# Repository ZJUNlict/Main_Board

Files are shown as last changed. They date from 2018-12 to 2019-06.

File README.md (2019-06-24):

# Main_Board

ZJUNlict Main Board Design for the RoboCup Soccer Small-Size League https://zjunlict.cn/

The main board is designed to replace the [core board](https://github.com/ZJUNlict/Core_Board), [mother board](https://github.com/ZJUNlict/Mother_Board) and [motor driver board](https://github.com/ZJUNlict/Motor_Driver_Board) which is currently under testing. (The board is designed using [Altium Designer](https://www.altium.com/altium-designer/) 17.1)

**Sincere thanks for Team TIGERs Mannheim's [opensource electronics design](https://tigers-mannheim.de/index.php?id=65), which gives a mature seperate BLDC controller design with small footprint and relative low cost.**

The photos of the main board are shown below.

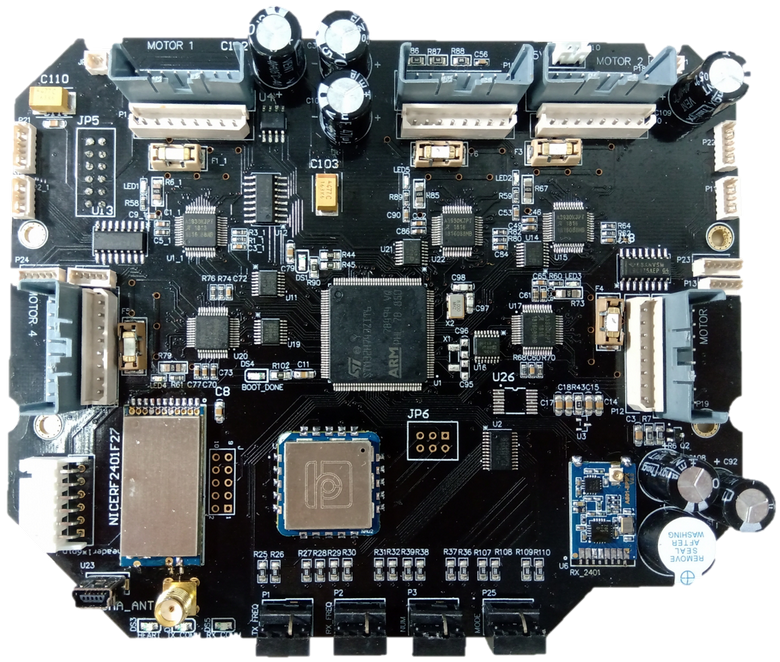
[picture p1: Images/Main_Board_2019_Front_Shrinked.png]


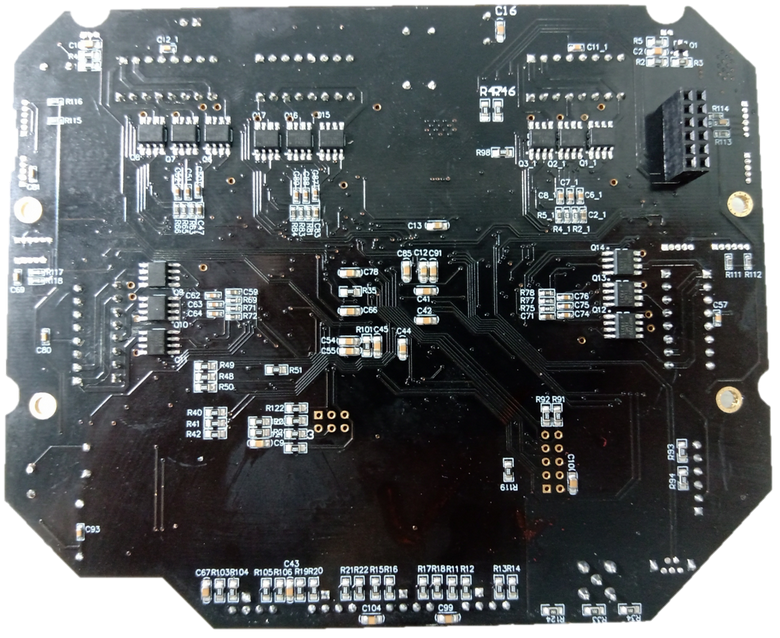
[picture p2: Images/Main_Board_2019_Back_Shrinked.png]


The main features are:

* STM32H743ZIT6 as the main controller with frequency up to 480MHz.
* Two nRF24L01P modules operate in different frequency handles package receiving and transmitting.
* An IO expansion chip PCA9539 reads rotary DIP switchs.
* Five BLDC controller chips A3930 controls five motors based on Team TIGERs Mannheim's design.
* Differential receiver chip SN65LBC175 receives encoder signal.
* AD converter chip ADS112C04IPWR process the current signal from A3930.
* Interface to external gyroscope, accelerometer, compass and optic flow chips. (IIC and SPI)

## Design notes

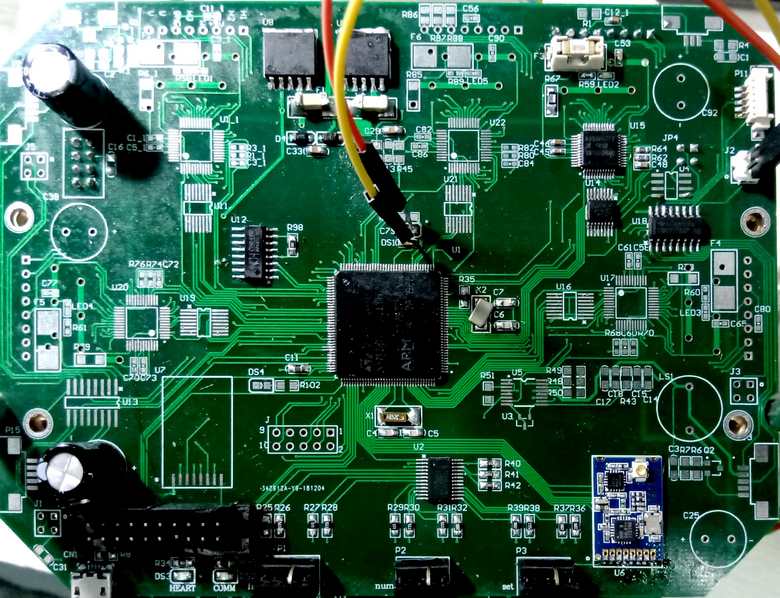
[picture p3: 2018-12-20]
Images/Main_Board_2_Shrinked.jpg

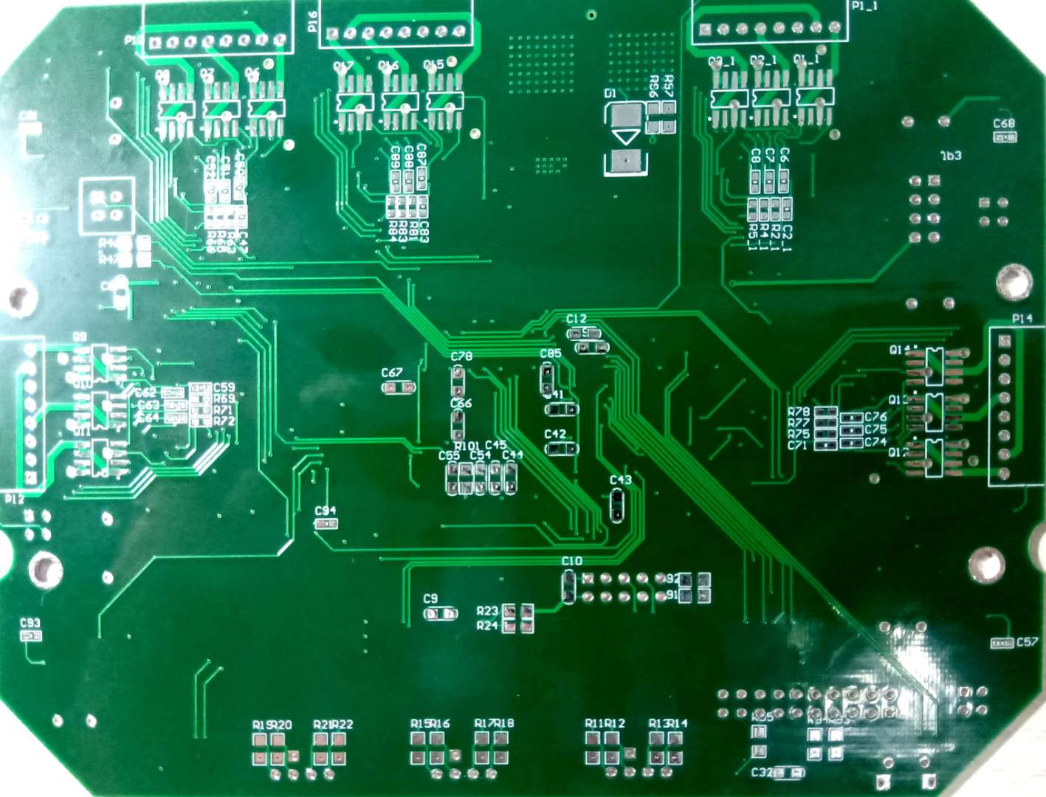
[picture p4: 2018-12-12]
Images/Main_Board_Back.jpg

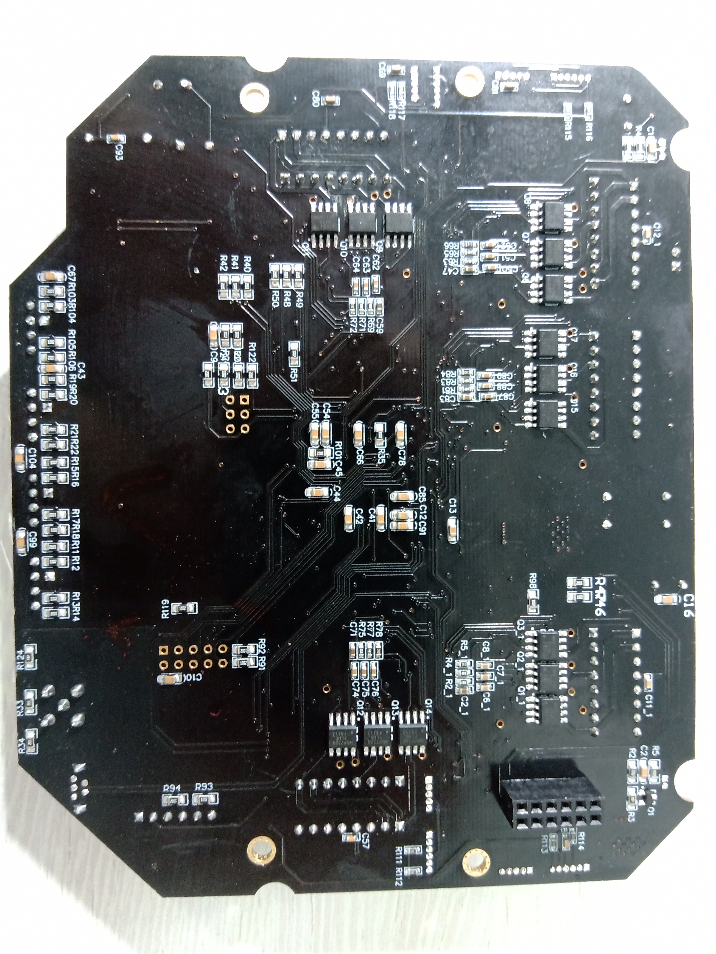
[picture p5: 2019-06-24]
Images/Main_Board_2019_Back.jpg

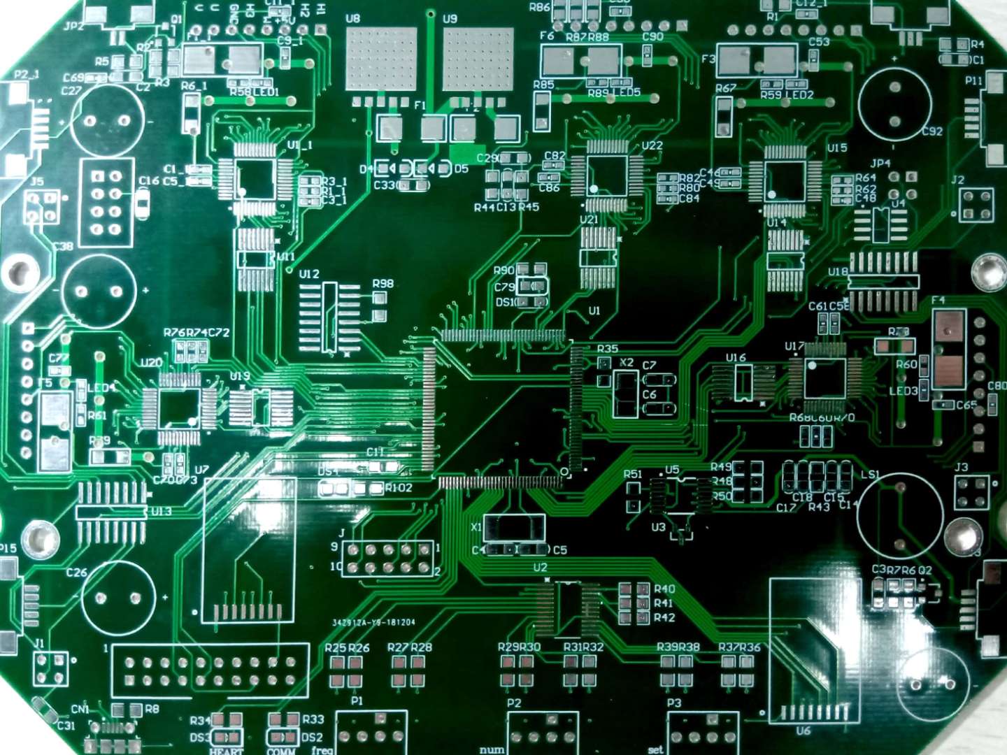
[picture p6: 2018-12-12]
Images/Main_Board_Front.jpg

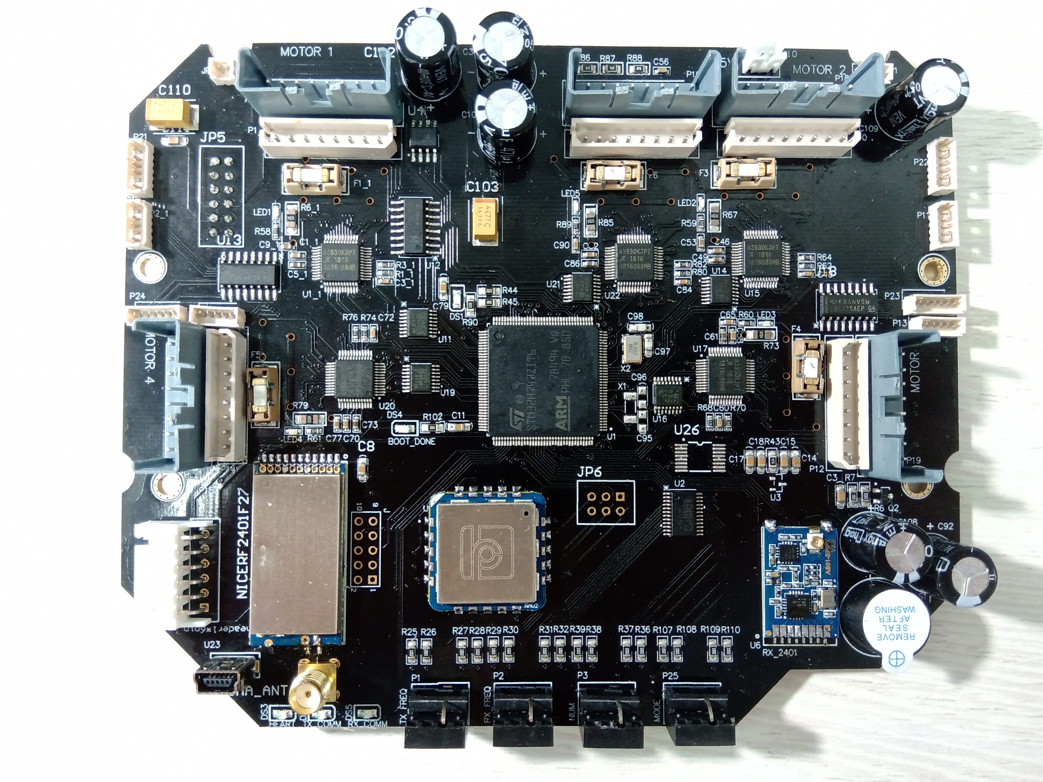
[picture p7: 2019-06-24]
Images/Main_Board_2019_Front.jpg

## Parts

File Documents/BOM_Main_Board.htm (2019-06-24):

Comment | Description | Designator | Footprint | LibRef | Quantity
0.1uf | Capacitor | C1, C2, C3, C8, C9, C10, C15, C16, C17, C18, C41, C42, C43, C44, C45, C54, C55, C66, C67, C78, C79, C85, C91, C99, C104, C111 | 0805C | Cap | 26
1uF | Capacitor | C1_1, C2_1, C9_1, C46, C47, C53, C58, C59, C65, C70, C71, C77, C82, C83, C90 | 0603C | Cap | 15
1nF | Capacitor | C3_1, C48, C60, C72, C84 | 0603C | Cap | 5
470nF | Capacitor | C5_1, C49, C61, C73, C86 | 0603C | Cap | 5
33nF | Capacitor | C6_1, C7_1, C8_1, C50, C51, C52, C62, C63, C64, C74, C75, C76, C87, C88, C89 | 0603C | Cap | 15
1uf | Capacitor | C11, C12, C14 | 0805C | Cap | 3
0.1uF | Capacitor | C11_1, C12_1, C56, C57, C68, C69, C80, C81, C93 | 0603C | Cap | 9
10uF | Capacitor | C13 | 0805C | Cap | 1
470uF | Polarized Capacitor (Radial) | C38, C92, C107, C108, C109, C112 | 470uF | Cap Pol1 | 6
2pf | Capacitor | C95, C96 | 0805C | Cap | 2
4.3pf | Capacitor | C97, C98 | 0805C | Cap | 2
CAP470 | 470uF电容贴片 | C103, C110 | CAPPM7360X200N | T523H477M016APE0707280 | 2
LED2 | Typical RED, GREEN, YELLOW, AMBER GaAs LED | DS1, DS3, DS4 | 0805D | LED2 | 3
LED1 | Typical RED, GREEN, YELLOW, AMBER GaAs LED | DS2, DS5 | 0805D | LED1 | 2
10A |  | F1_1, F3, F4, F5, F6 | FUSE_HEADER | FUSE | 5
header1*6pin | header1*6pin | header1*6pin | 1*6_2.5mm | header1*6pin | 1
10 |  | J | 10 | 10 | 1
1*2*2.5mm |  | J10 | 1*2_2.5mm | 1*2*2.5mm | 1
Header 3 | Header, 3-Pin | JP1 | SHDR3 | Header 3 | 1
Header 2 | Header, 2-Pin | JP2 | SHDR2 | Header 2 | 1
Header 4X2 | Header, 4-Pin, Dual row | JP5 | 2*6_2.5mm | Header 6X2 | 1
header6pin |  | JP6 | 2*3_2.5mm | header6pin | 1
led |  | LED1, LED2, LED3, LED4, LED5 | 0603_diode | led | 5
Buzzer | Buzzer | LS1 | Buzzer | Buzzer | 1
NICERF2401F27 |  | NICERF2401F27 | NICERF2401F27 | NICERF2401F27 | 1
COAX-M | RF Coaxial PCB Connector, MMCX; Thru-Hole, Vertical Mount Plug, 50 Ohm Impedance | P1, P2, P3, P25 | A6RV-161RS | COAX-M | 4
Header_8P | Used for Motor connection in ZJUNlict | P1_1, P8, P10, P12, P14 | 8P - WF25122 | Header_8P | 5
Header 5 | Header, 5-Pin | P2_1, P11, P13, P15 | SHDR5 | Header 5 | 4
安装孔 | Plug | P4, P5, P6, P7 | 安装孔-3.5-5 | Plug | 4
Header_8P | Used for Motor connection in ZJUNlict | P16, P17, P18, P19, P20 | SHDR8 | Header_8P | 5
Header 5 | Header, 5-Pin | P21, P22, P23, P24 | SHDR6 | Header 6 | 4
9013 | NPN General Purpose Amplifier | Q1, Q2 | SO-G3/Y1 | BC817-40 | 2
IRF8313 |  | Q1_1, Q2_1, Q3_1, Q6, Q7, Q8, Q9, Q10, Q11, Q12, Q13, Q14, Q15, Q16, Q17 | so-8 bg | SO-8 IRF8313 | 15
20K | Resistor | R1 | 0805R | Res1 | 1
47K | Resistor | R1_1, R62, R68, R74, R80 | 0603R | Res1 | 5
2.2K | Resistor | R2, R6 | 0805R | Res1 | 2
100K | Resistor | R2_1, R4_1, R63, R65, R69, R71, R75, R81, R83 | 0603R | Res1 | 9
1K | Resistor | R3, R7 | 0805R | Res1 | 2
10K | Resistor | R3_1, R5_1, R64, R66, R70, R72, R76, R78, R82, R84, R111, R112, R113, R114, R115, R116, R117, R118 | 0603R | Res1 | 18
100 | Resistor | R4 | 0805R | Res1 | 1
300 | Resistor | R5 | 0805R | Res1 | 1
0.02 | Resistor | R6_1, R67, R73, R79, R85 | 1206 10A | Res1 | 5
10k | Resistor, Resistor, Resistor, Resistor, Resistor, Resistor, Resistor, Resistor, Resistor, Resistor, Resistor, Resistor, Resistor, Resistor, Resistor, Resistor, Resistor, Resistor, Resistor, Resistor, Resistor, Resistor, Resistor, Resistor, Resistor, Resistor, Resistor, Resistor, Resistor, Resistor, Resistance, Resistance, Resistor, Resistor, Resistor, Resistor, Resistor, Resistor, Resistor, Resistor, Resistor, Resistor, Resistor, Resistor, Resistor, Resistor, Resistor, Resistor, Resistor, Resistor, Resistor, Resistor, Resistor, Resistor, Resistor | R11, R12, R13, R14, R15, R16, R17, R18, R19, R20, R21, R22, R23, R24, R25, R26, R27, R28, R29, R30, R31, R32, R35, R36, R37, R38, R39, R40, R41, R42, R46, R47, R48, R49, R50, R51, R91, R92, R93, R94, R98, R101, R103, R104, R105, R106, R107, R108, R109, R110, R119, R120, R121, R122, R123 | 0805R | Res1, Res1, Res1, Res1, Res1, Res1, Res1, Res1, Res1, Res1, Res1, Res1, Res1, Res1, Res1, Res1, Res1, Res1, Res1, Res1, Res1, Res1, Res1, Res1, Res1, Res1, Res1, Res1, Res1, Res1, SR0805, SR0805, Res1, Res1, Res1, Res1, Res1, Res1, Res1, Res1, Res1, Res1, Res1, Res1, Res1, Res1, Res1, Res1, Res1, Res1, Res1, Res1, Res1, Res1, Res1 | 55
3.3k | Resistor | R33, R34, R45, R90, R102, R124 | 0805R | Res1 | 6
470 | Resistor | R43 | 0805R | Res1 | 1
22k | Resistor | R44 | 0805R | Res1 | 1
10k |  | R58, R59, R60, R61, R89 | 0603 | res | 5
150K | Resistor | R77 | 0603R | Res1 | 1
5.1k |  | R86, R87, R88 | 0805 | res | 3
SMA_ANT |  | SMA_ANT | SMA_ANT | SMA_ANT | 1
MCU_LQFP144 |  | U1 | LQFP144_0R5_SKT | MCU_LQFP144 | 1
A3930 |  | U1_1, U15, U17, U20, U22 | LQFP-48 | LQFP 48 | 5
PCA9539_PW_24 | Remote 16-Bit I2C And SMBus, Low-Power I/O Expander With Interrupt Output, Reset & Config. Registers | U2 | PW24-L_pca9539 | PCA9539_PW_24 | 1
TL4050A10_DBZ_3 | Precision Micropower Shunt Voltage Reference | U3 | DBZ3-L | TL4050A10_DBZ_3 | 1
MC34152D | High Speed Dual MOSFET Driver | U4 | SO-G8 | MC34152D | 1
NRF2401P+ |  | U6 | NRF2401P+_zeyao | NRF2401P+ | 1
ADUM141D0BRQZ | Imported | U11, U14, U16, U19, U21 | RQ_16 | ADUM141D0BRQZ | 5
CH340B |  | U12 | SOP16 | CH340B | 1
SN65LBC175A-EP_16 | Quadruple 2-Input Positive-NAND Gates | U13, U18 | SOP16 | SN65LBC175A-EP_16 | 2
miniusb |  | U23 | miniusb 180 | miniusb | 1
LPMS-NAV2 | LPMS-NAV2 | U25 | LPMS-NAV2 | LPMS-NAV2 | 1
ADS112C04IPWR | Imported | U26 | TSSOP_PW0016A_ADS112C04 | ADS112C04IPWR | 1
32.768KHZ | Crystal | X1 | FC-255 | CRYSTAL | 1
8MHZ | Crystal or Oscillator | X2 | 5032 | ECS-80-18-30B-AGN-TR | 1

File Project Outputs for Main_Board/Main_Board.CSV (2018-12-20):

Bill of Material for
On 2018/12/20 at 20:23:41
Comment | Pattern | Quantity | Components
0.02 | 1206 10A | 5 | R6_1, R67, R73, R79, R85 | Resistor
0.1uF | 0603C | 10 | C11_1, C12_1, C56, C57, C68, C69, C80, C81, C93, C94 | Capacitor
0.1uF | 0805C | 33 | C2, C3, C4, C5, C6, C7, C8, C9, C10, C11, C12, C13, C15, C16, C17, C18, C29, C31, C32, C33, C41, C42, C43, C44, C45, C54, C55, C66, C67, C78, C79, C85, C91 | Capacitor
10 | 10 | 1 | J
100 | 0805R | 1 | R4 | Resistor
100K | 0603R | 5 | R2_1, R63, R69, R75, R81 | Resistor
1050170001 | Micro_USB | 1 | CN1
10A | FUSE_HEADER | 5 | F1_1, F3, F4, F5, F6
10K | 0603R | 10 | R3_1, R5_1, R64, R66, R70, R72, R76, R78, R82, R84 | Resistor
10K | 0805R | 46 | R8, R11, R12, R13, R14, R15, R16, R17, R18, R19, R20, R21, R22, R23, R24, R25, R26, R27, R28, R29, R30, R31, R32, R35, R36, R37, R38, R39, R40, R41, R42, R46, R47, R48, R49, R50, R51, R91, R92, R93, R94, R95, R96, R97, R98, R101 | Resistor
150K | 0603R | 5 | R4_1, R65, R71, R77, R83 | Resistor
1K | 0805R | 2 | R3, R7 | Resistor
1nF | 0603C | 5 | C3_1, C48, C60, C72, C84 | Capacitor
1uF | 0603C | 15 | C1_1, C2_1, C9_1, C46, C47, C53, C58, C59, C65, C70, C71, C77, C82, C83, C90 | Capacitor
1uF | 0805C | 1 | C14 | Capacitor
2.2K | 0805R | 2 | R2, R6 | Resistor
20 | 20SWD | 1 | 1
20K | 0805R | 3 | R1, R90, R102 | Resistor
22k | 0805R | 1 | R44 | Resistor
3.3k | 0805R | 1 | R45 | Resistor
300 | 0805R | 1 | R5 | Resistor
32.768KHZ | FC255_32.768K | 1 | X1 | Crystal
33nF | 0603C | 15 | C6_1, C7_1, C8_1, C50, C51, C52, C62, C63, C64, C74, C75, C76, C87, C88, C89 | Capacitor
3A | 2512r | 2 | F1, F2 | Resistor
4.7K | 603 | 5 | R58, R59, R60, R61, R89
4.7K | 805 | 3 | R86, R87, R88
4.7uF | 0805C | 1 | C1 | Capacitor
4 | 4 | 4 | J1, J2, J3, J5
470 | 0805R | 1 | R43 | Resistor
470nF | 0603C | 5 | C5_1, C49, C61, C73, C86 | Capacitor
470uF | 470uF | 5 | C25, C26, C27, C38, C92 | Capacitor
47K | 0603R | 5 | R1_1, R62, R68, R74, R80 | Resistor
510 | 0805R | 2 | R33, R34 | Resistor
8MHZ | 5320_8M | 1 | X2 | Crystal
9013 | SO-G3/Y1 | 2 | Q1, Q2 | NPN General Purpose Amplifier
A3930 | LQFP-48 | 5 | U1_1, U15, U17, U20, U22
ADS112C04IPWR | TSSOP_PW0016A_ADS112C04 | 1 | U5 | Imported
ADUM141D0BRQZ | RQ_16 | 5 | U11, U14, U16, U19, U21 | Imported
BA33DD0WHFP | HRP5_16TO5 | 1 | U9
BA50DD0WHFP | HRP5_16TO5 | 1 | U8
Buzzer | Buzzer | 1 | LS1 | Buzzer
CH340B | SOP16 | 1 | U12
COAX-M | A6RV-161RS | 3 | P1, P2, P3 | RF Coaxial PCB Connector, MMCX; Thru-Hole, Vertical Mount Plug, 50 Ohm Impedance
Header 2 | SMD-2P-1.25 | 1 | JP2 | Header, 2-Pin
Header 2X2 | 2*2_2.5mm | 1 | JP4 | Header, 2-Pin, Dual row
Header 3 | SMD-3P-1.25 | 1 | JP1 | Header, 3-Pin
Header 4X2 | 2*4_2.5mm | 1 | JP3 | Header, 4-Pin, Dual row
Header 5 | SMD-5P-1.25 | 4 | P2_1, P11, P13, P15 | Header, 5-Pin
Header_8P | Header_8P | 5 | P1_1, P10, P12, P14, P16 | Used for Motor connection in ZJUNlict
IRF8313 | so-8 bg | 15 | Q1_1, Q2_1, Q3_1, Q6, Q7, Q8, Q9, Q10, Q11, Q12, Q13, Q14, Q15, Q16, Q17
led | 0603_diode | 5 | LED1, LED2, LED3, LED4, LED5
LED1 | 0805D | 1 | DS2 | Typical RED, GREEN, YELLOW, AMBER GaAs LED
LED2 | 0805D | 3 | DS1, DS3, DS4 | Typical RED, GREEN, YELLOW, AMBER GaAs LED
MBR120VLSFT1G SOD123 | sod123 | 2 | D4, D5 | Default Diode
MC34152D | SO-G8 | 1 | U4 | High Speed Dual MOSFET Driver
MCU_LQFP144 | LQFP144_0R5_SKT | 1 | U1
NRF2401P+ | NRF2401P+_zeyao | 2 | U6, U7
PCA9539_PW_24 | PW24-L_pca9539 | 1 | U2 | Remote 16-Bit I2C And SMBus, Low-Power I/O Expander With Interrupt Output, Reset & Config. Registers
SN65LBC175A-EP_16 | SOP16 | 2 | U13, U18 | Quadruple 2-Input Positive-NAND Gates
SS36 | SMC | 1 | D1 | Default Diode
TL4050A10_DBZ_3 | DBZ3-L | 1 | U3 | Precision Micropower Shunt Voltage Reference
 |  |  |  | Plug

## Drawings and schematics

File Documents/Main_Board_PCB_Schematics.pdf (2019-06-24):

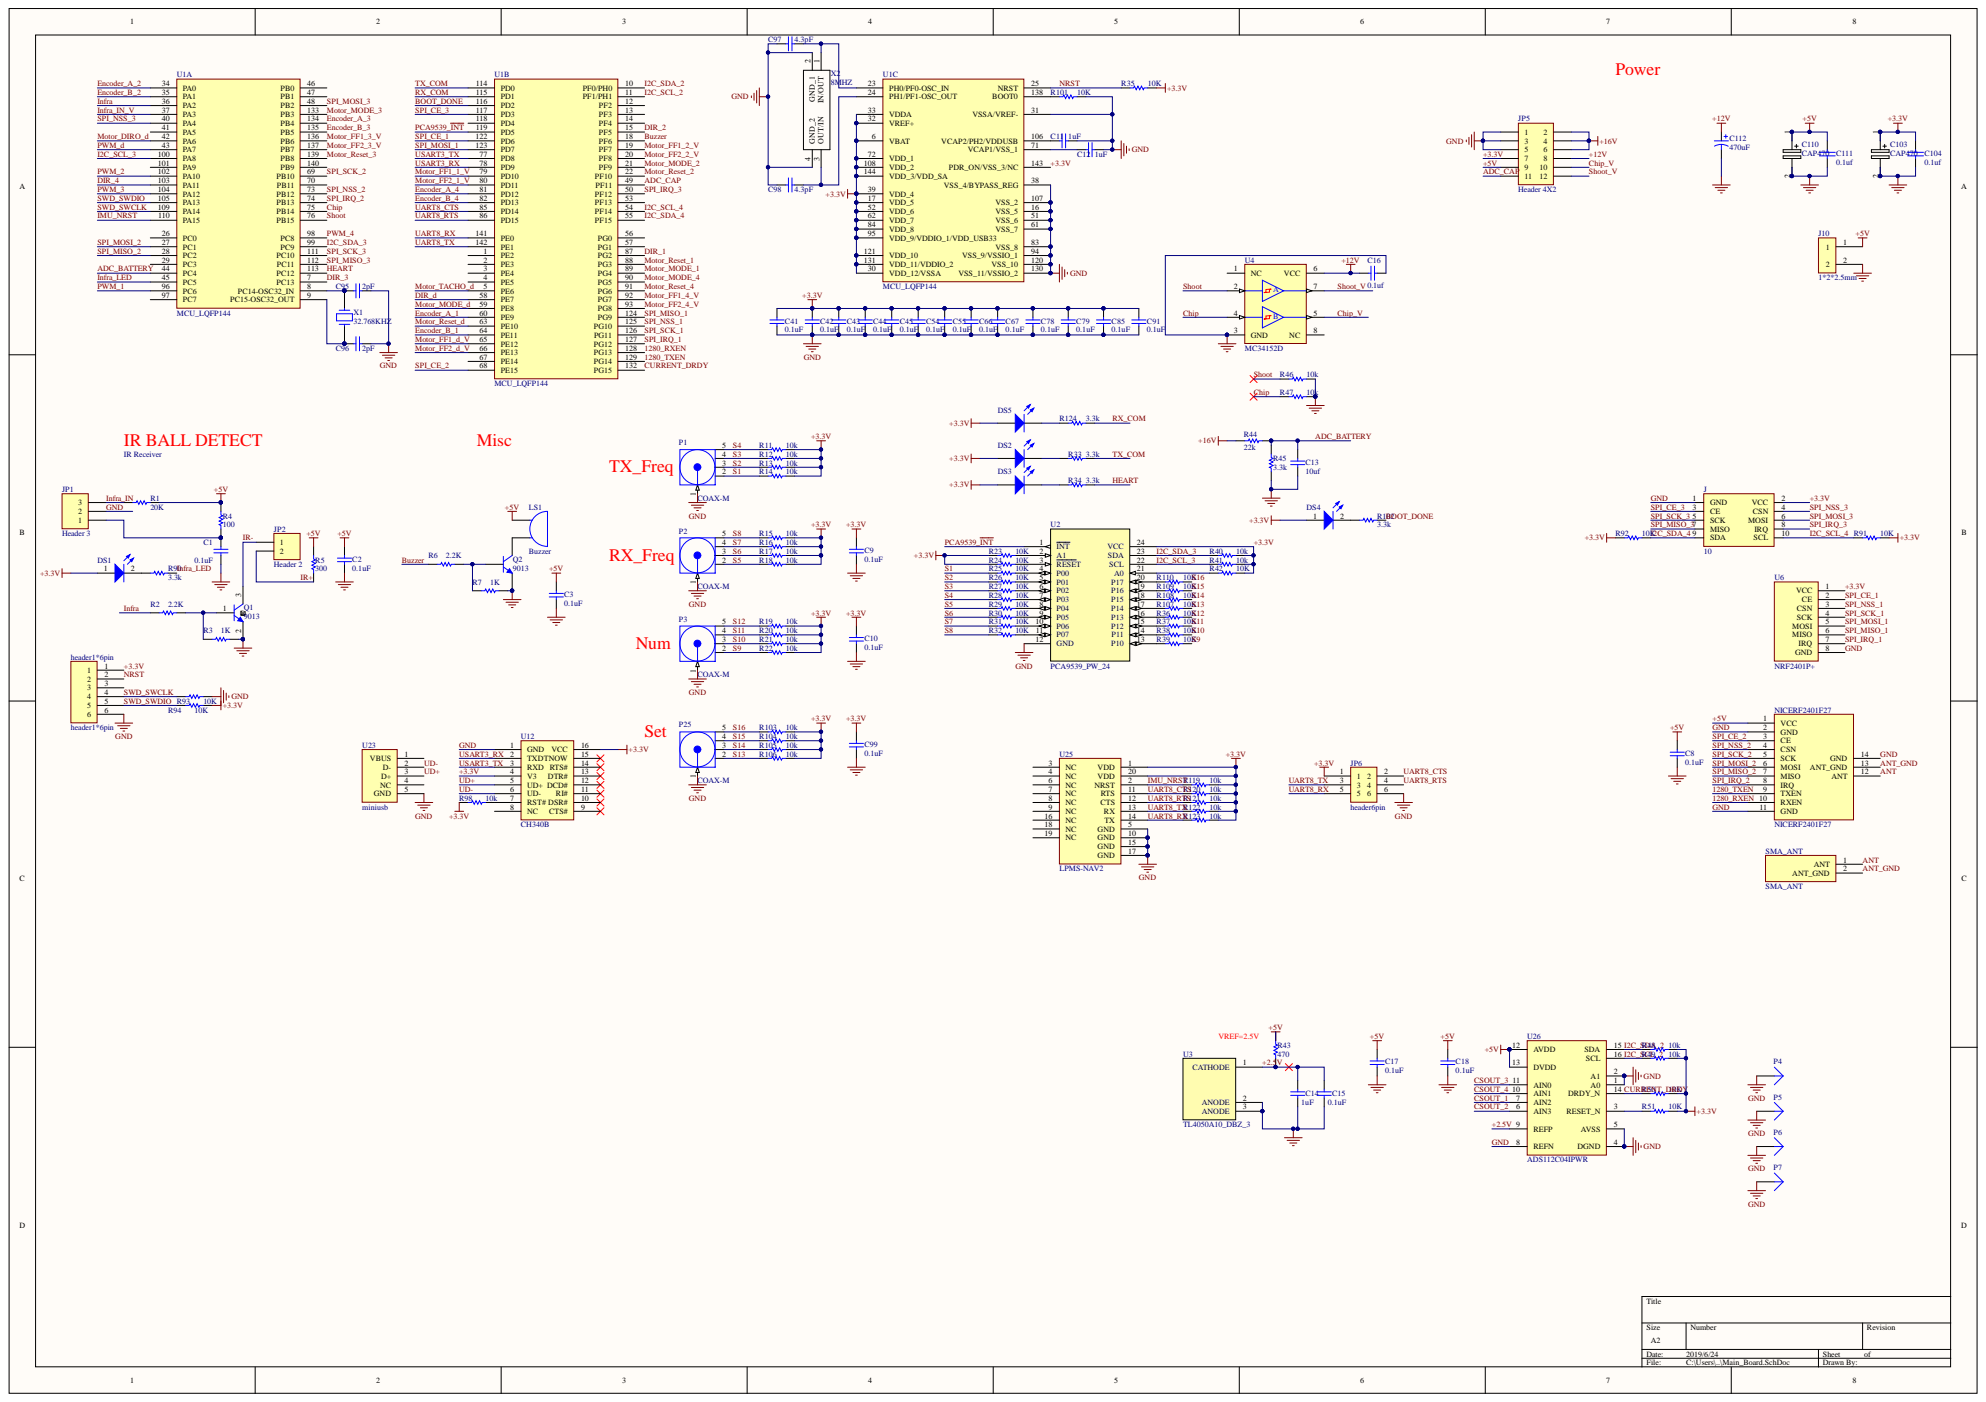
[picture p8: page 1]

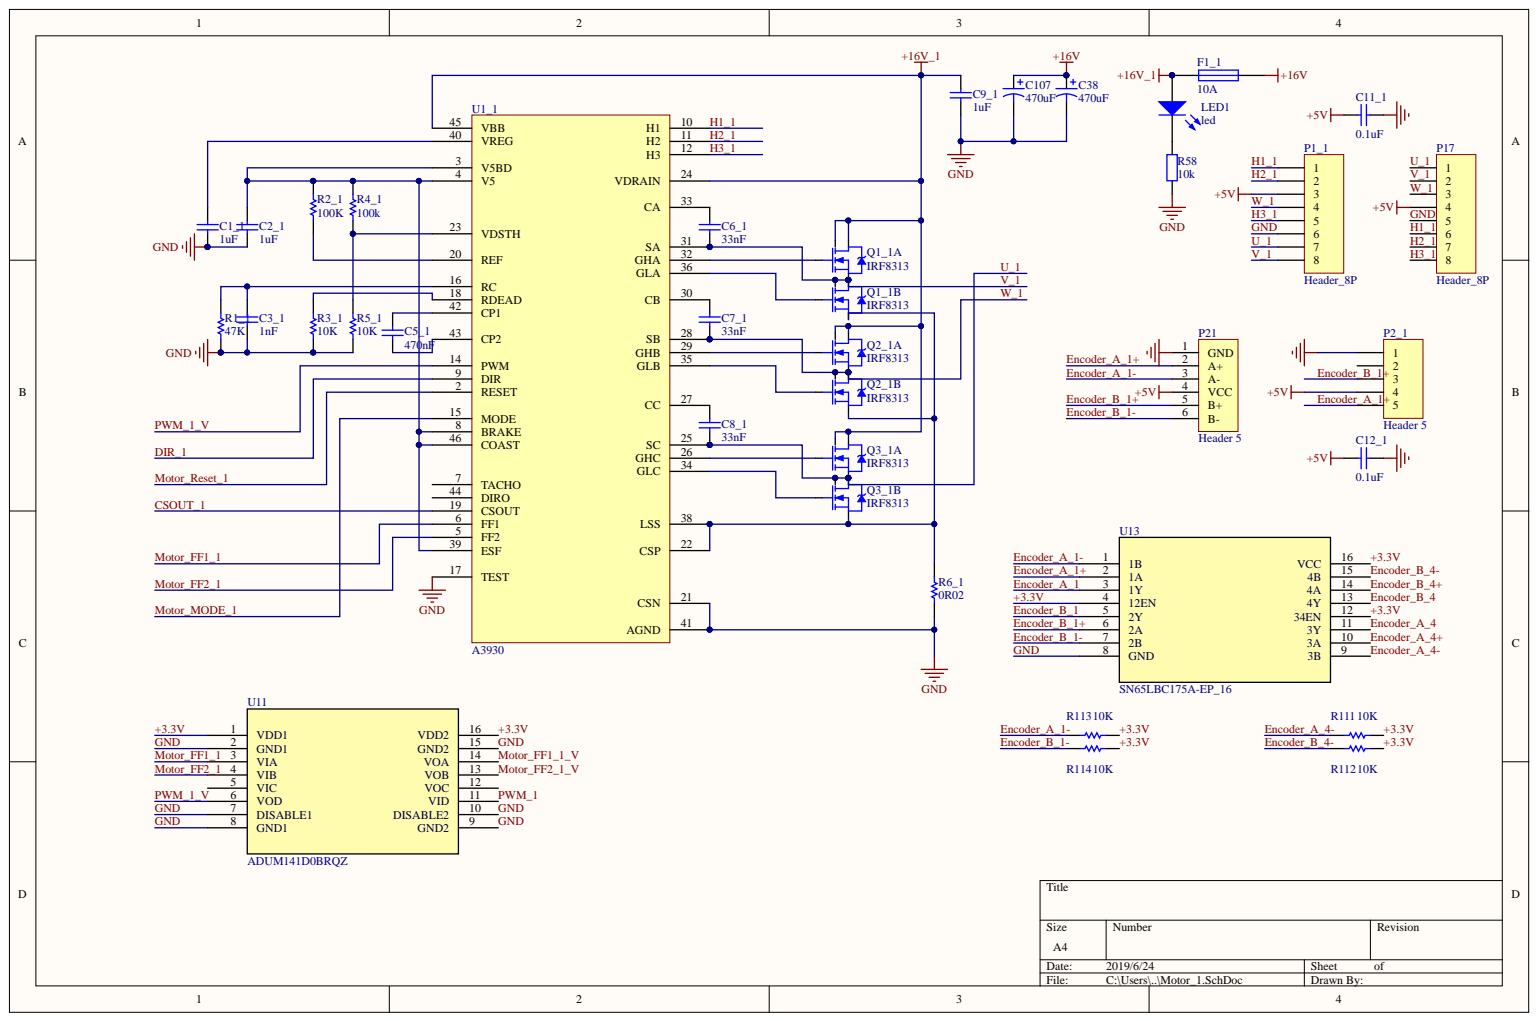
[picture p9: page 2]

V5BD 3
V5 4

R2_1 R4_1 | | VDSTH 23

REF 20

PWM_1_V | BRAKE 8
DIR_1 | COAST 46

Motor_Reset_1
CSOUT_1 | DIRO 44

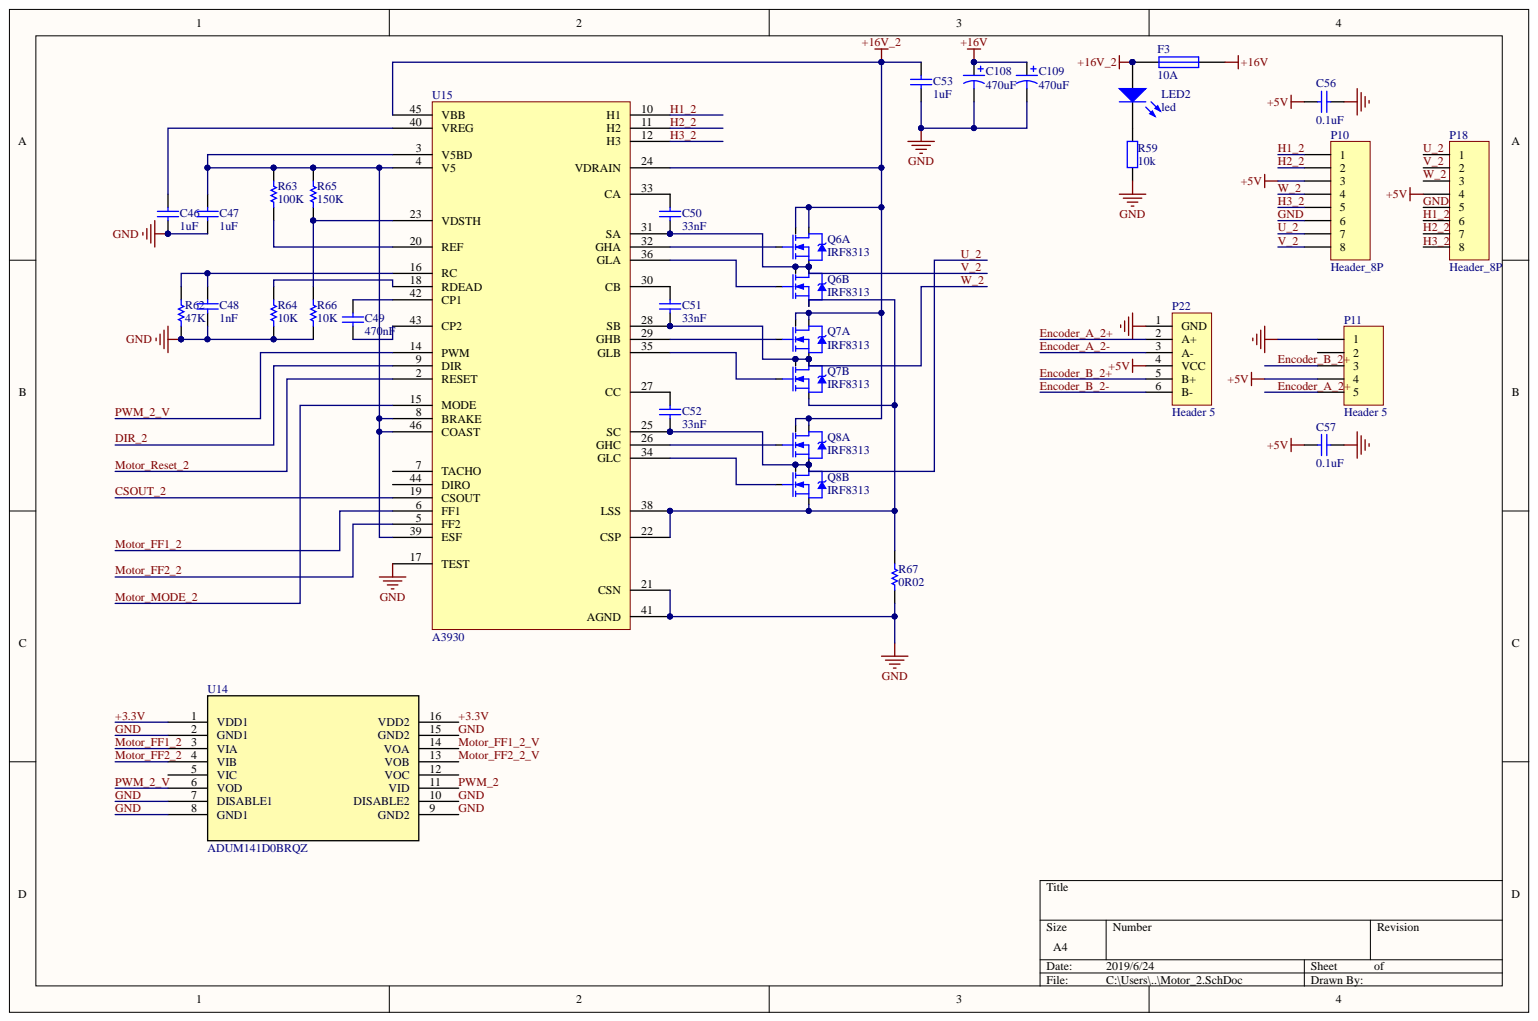
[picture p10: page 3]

R63 | R65 | VDSTH 23

REF 20

PWM_2_V | 8

COAST 46 TACHO 7

DIR_2

Motor_Reset_2
CSOUT_2 | | DIRO 44

Motor_FF1_2 | | ESF 39

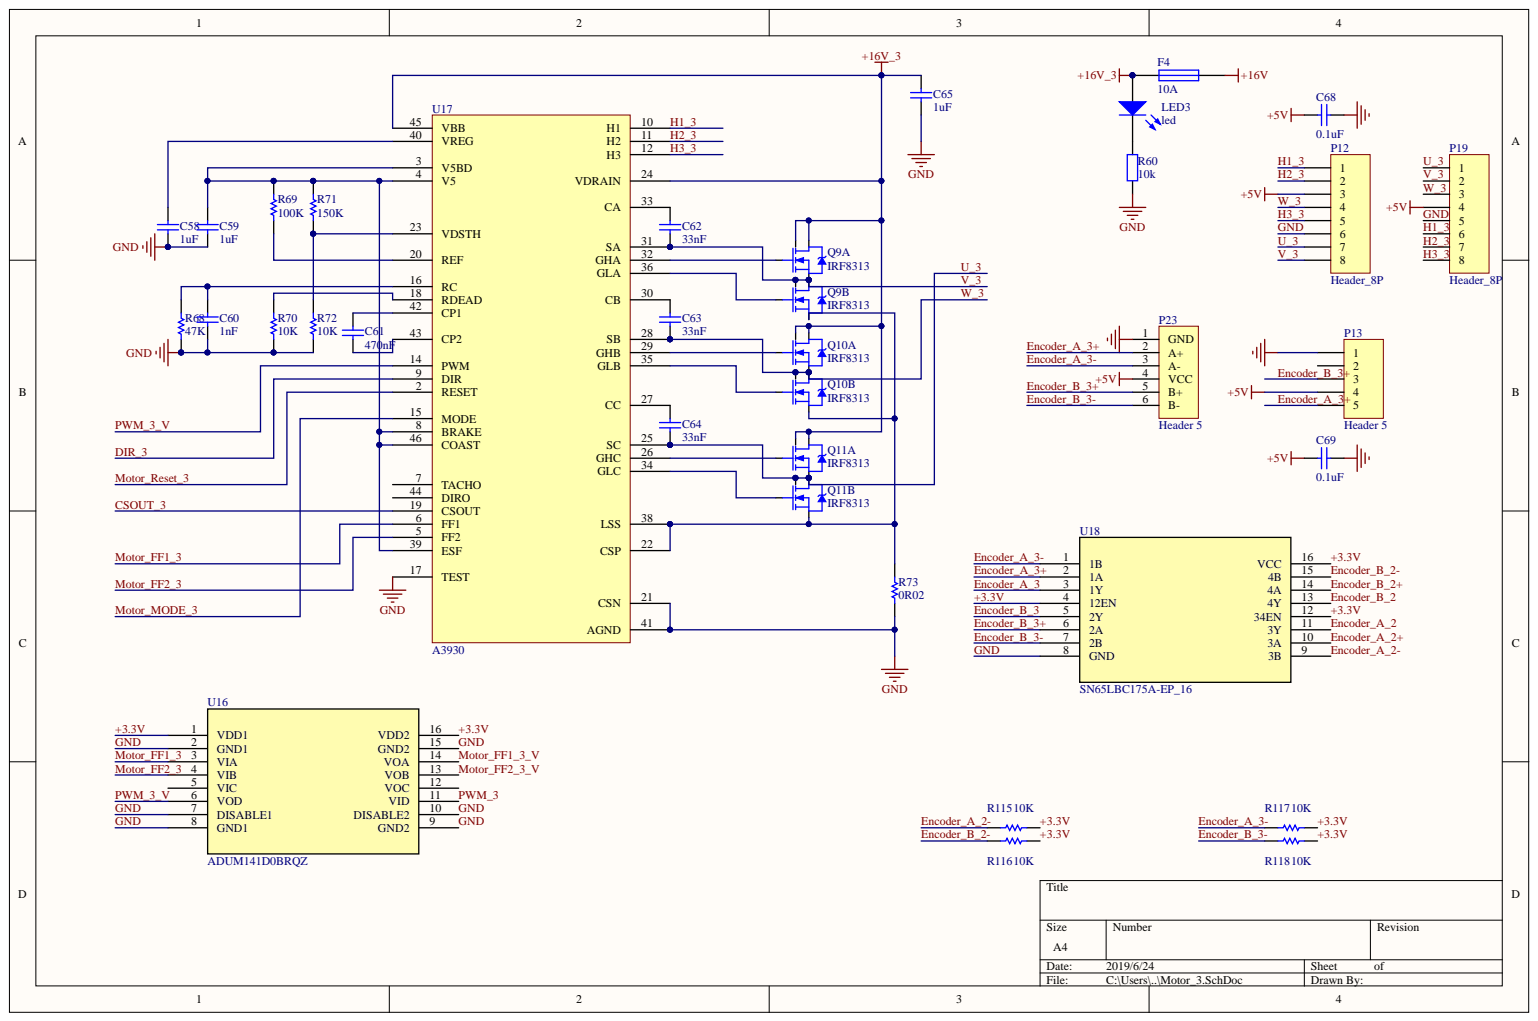
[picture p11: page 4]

R69 R71 | | VDSTH 23

REF 20

PWM_3_V | 8

COAST 46 TACHO 7

DIR_3

Motor_Reset_3
CSOUT_3 | | DIRO 44

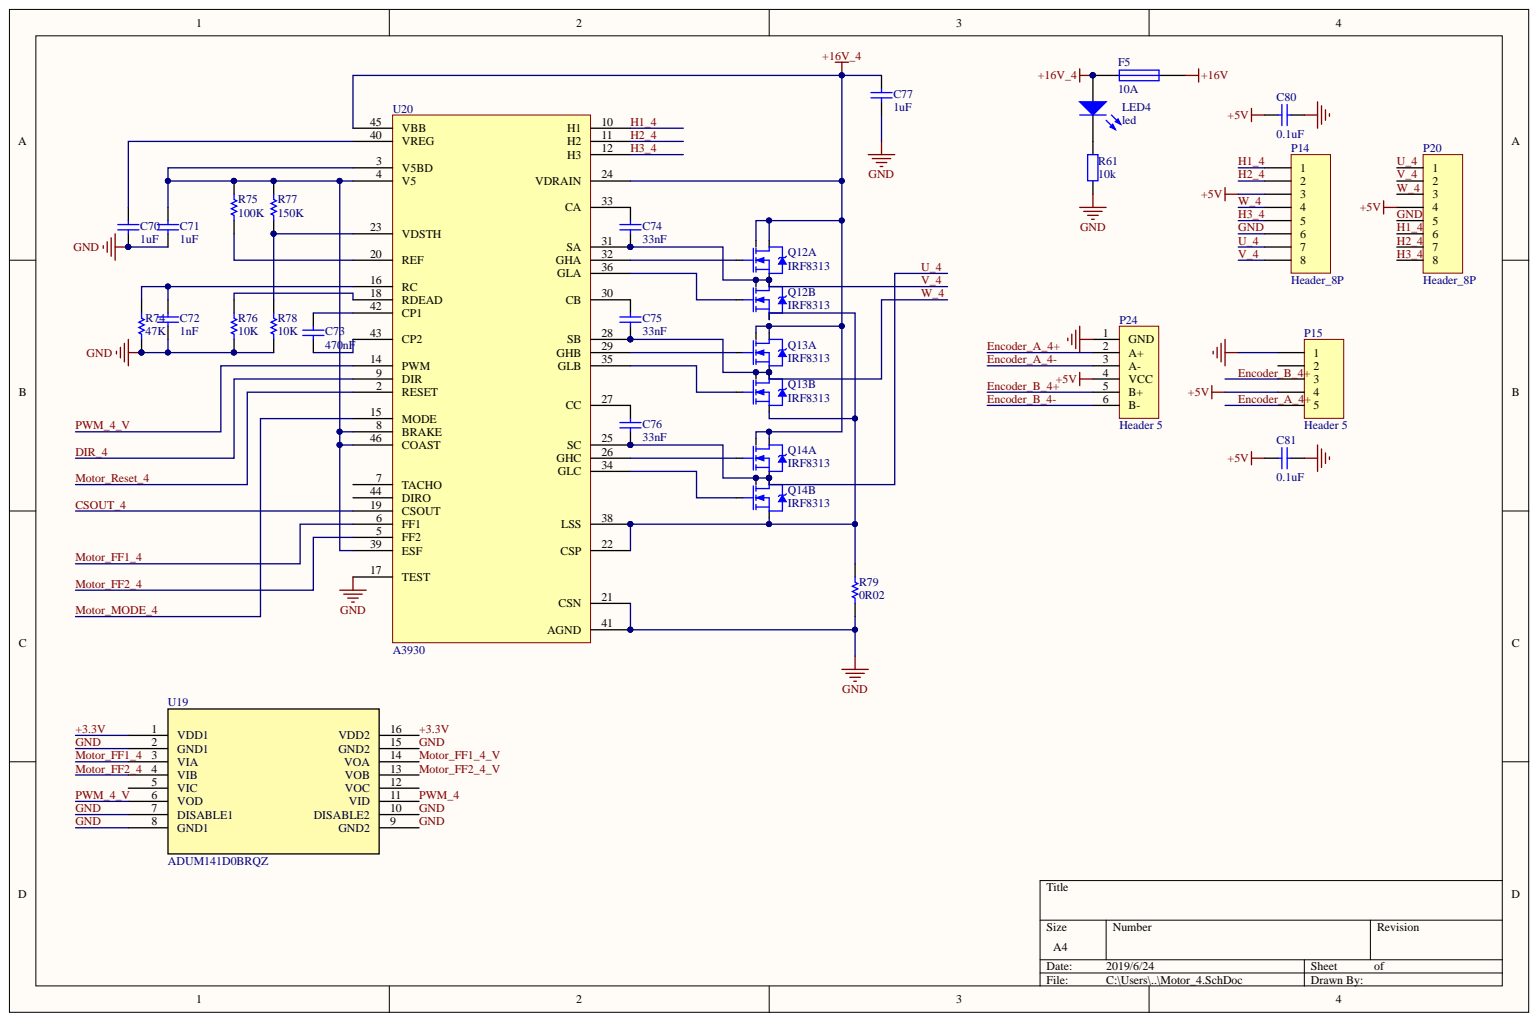
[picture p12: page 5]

R75 R77 | | VDSTH 23

REF 20

PWM_4_V | 8

COAST 46 TACHO 7

DIR_4

Motor_Reset_4
CSOUT_4 | | DIRO 44

Motor_FF1_4 | | ESF 39

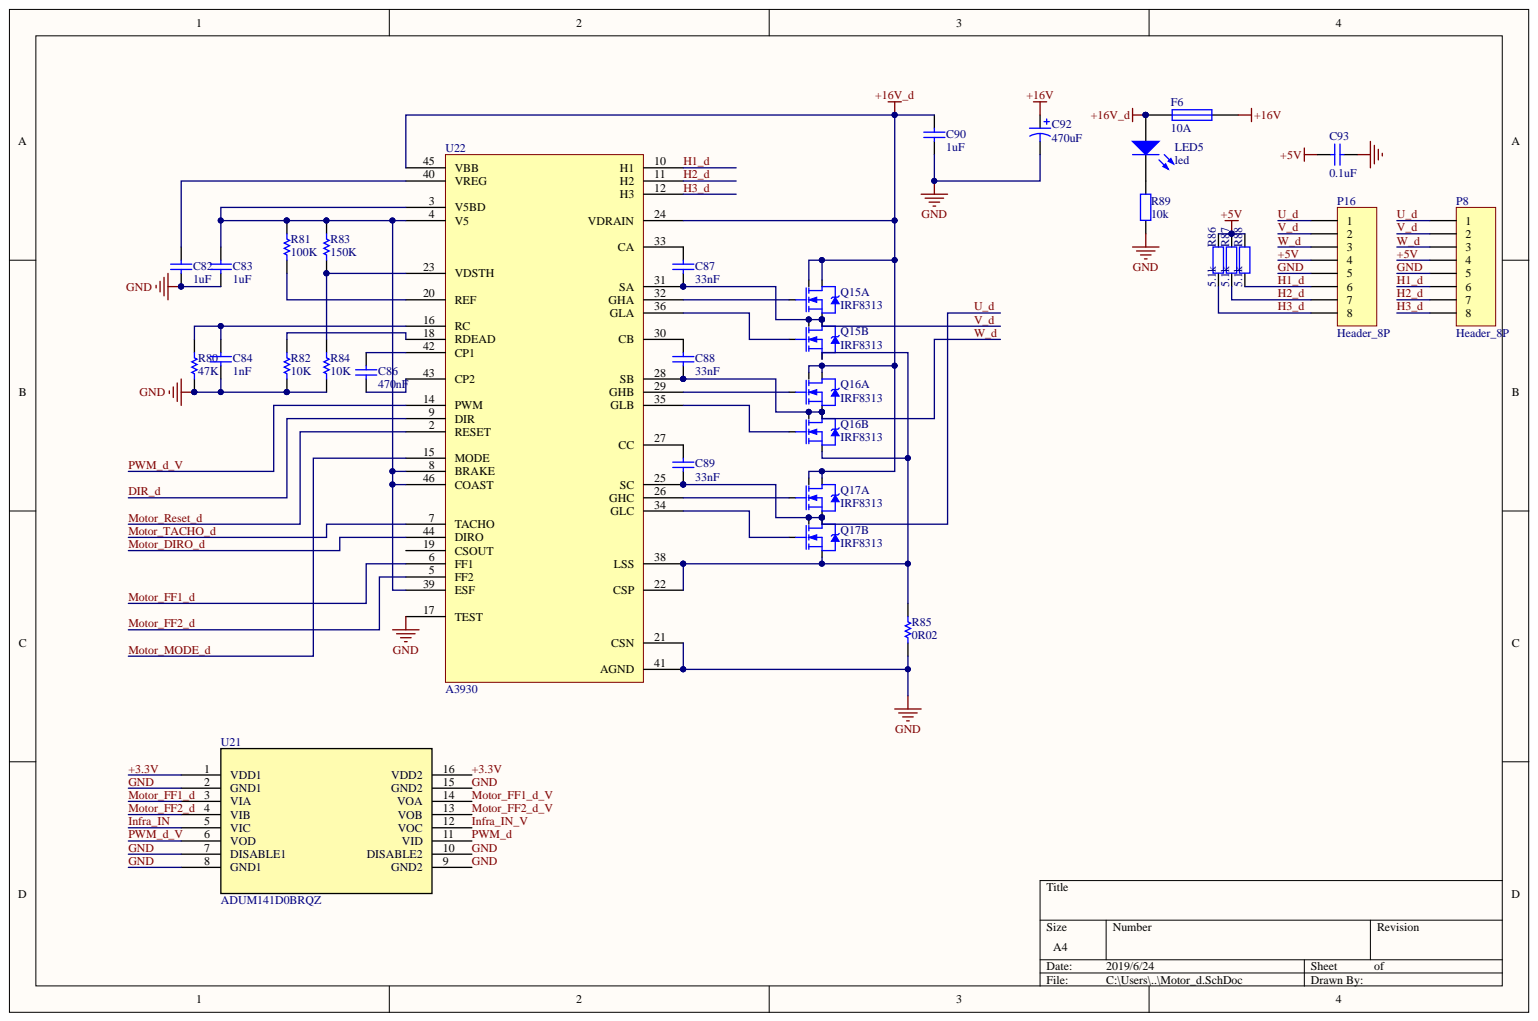
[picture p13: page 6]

REF 20

470nF | PWM 14

PWM_d_V | 8

COAST 46 TACHO 7

DIR_d

Motor_Reset_d
Motor_TACHO_d | | DIRO 44
Motor_DIRO_d | | CSOUT 19

Motor_FF1_d | | ESF 39

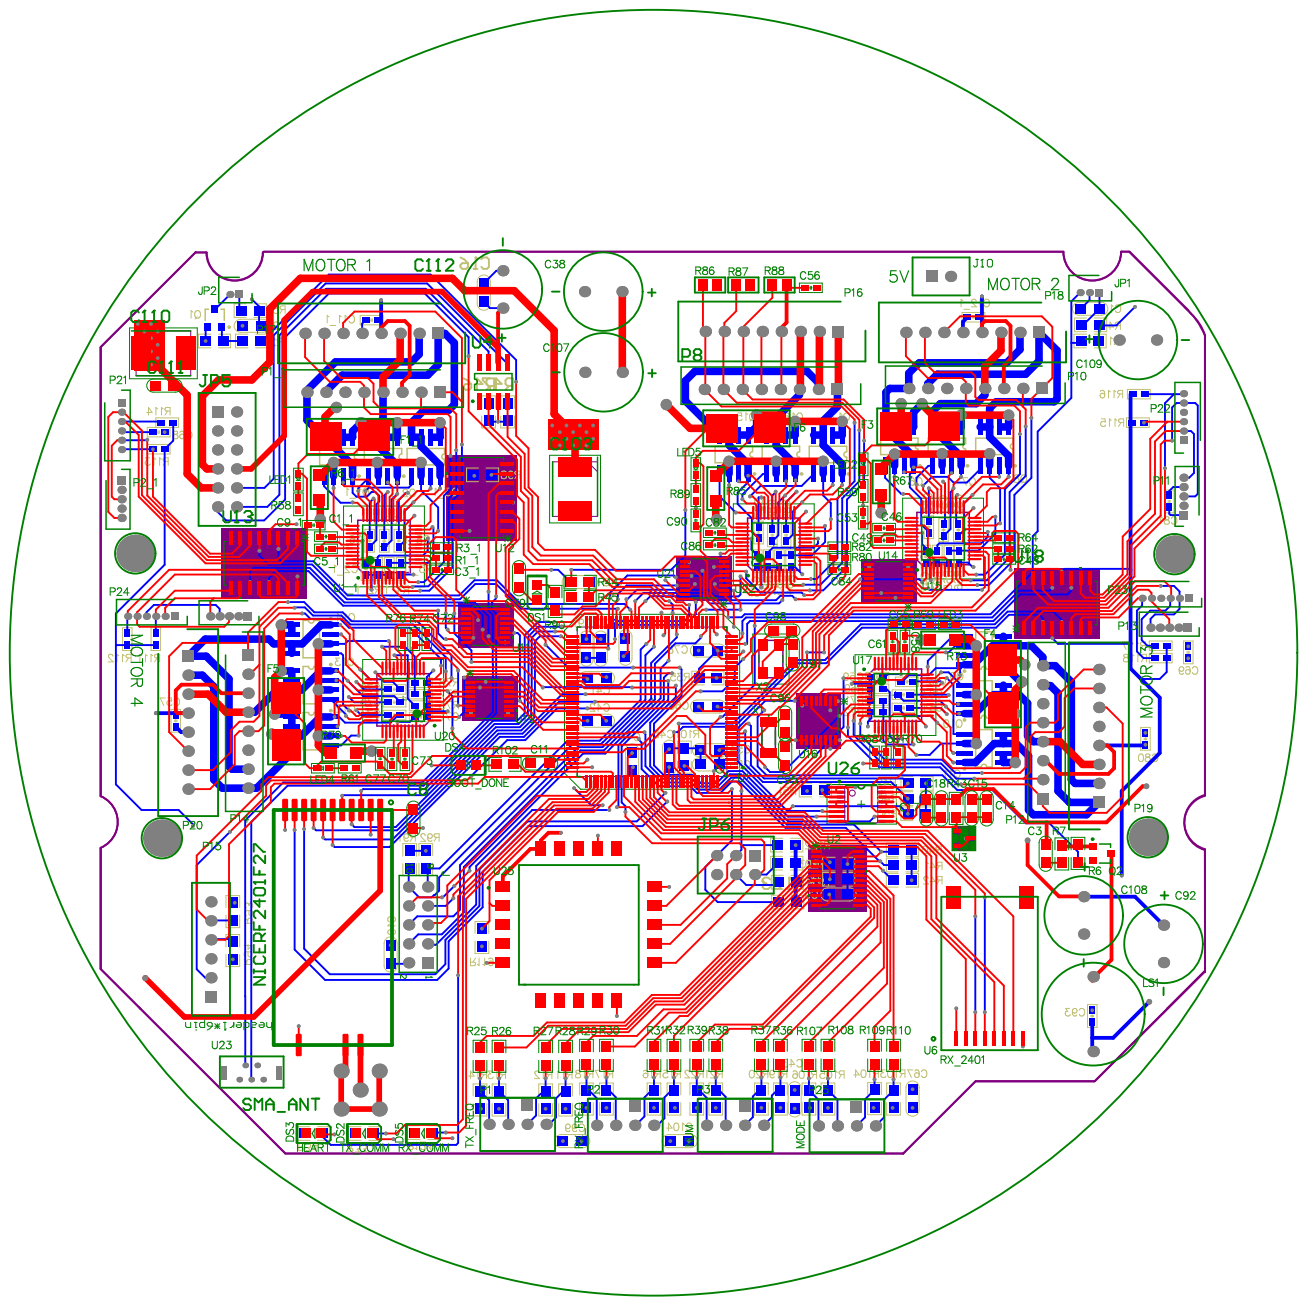
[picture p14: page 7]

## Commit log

2018-12-12 Add PCB files
    [Copy of Main_Board.PcbDoc, Copy of Main_Board.PcbLib, Main_Board.PcbLib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]
2018-12-20 Add BOM List and Readme
    [Main_Board.CSV, Main_Board.PrjPCB, Main_Board_BOM.CSV.xlsx]
2019-06-24 Update to RoboCup 2019 Version
    [Copy of Main_Board.PcbDoc, Main_Board.PcbLib, Main_Board.PrjPCB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]
